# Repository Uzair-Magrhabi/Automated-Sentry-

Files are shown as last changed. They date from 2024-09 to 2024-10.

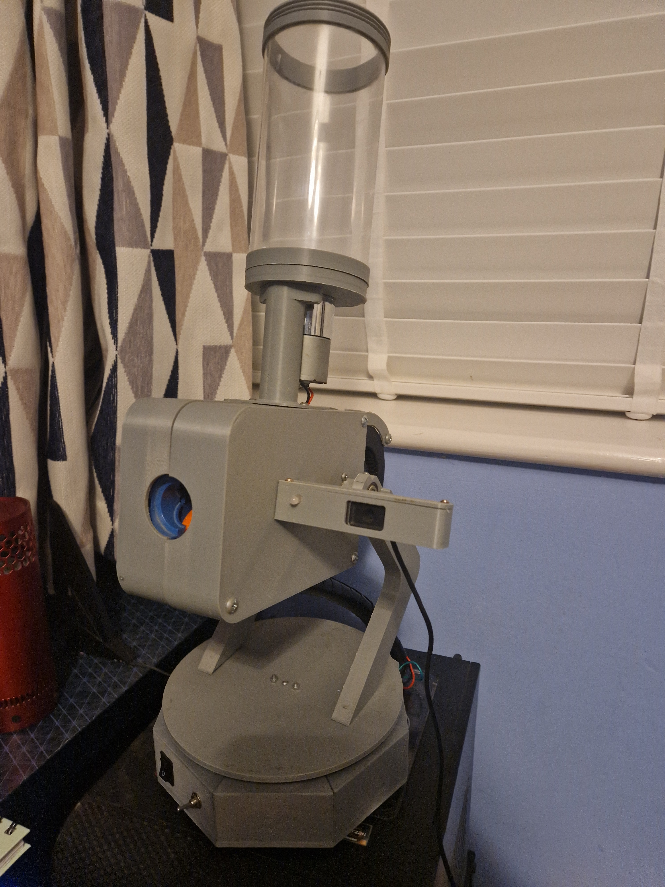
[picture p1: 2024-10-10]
20241010_222017.jpg

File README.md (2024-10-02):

Automated Sentry System
Using Fusion 360, I designed the primary firing mechanism for the turret. The propulsion system utilises flywheels, adapted from a Nerf blaster, to launch foam projectiles. A 5V blower fan is employed to feed the projectiles into the flywheels, guided by a custom-designed pipe, also created in Fusion 360. To manage projectile flow and prevent blockages, a 5V mini servo is integrated into the firing component, controlling the entry of rounds into the chamber.

The projectiles are stored in a hopper positioned above the main chassis, which can be easily refilled via a screwable lid. A custom-built propellor which acts as an agitator, attached to a coupler and powered by a high-torque DC motor, pushes the projectiles into the firing chamber when the mini servo is retracted. The hopper enclosure is transparent, allowing visual monitoring of the remaining ammunition.

Mounted on the main chassis is a camera holder, crucial for running object detection algorithms. The holder also contains an RGB LED, soldered to a PCB with the appropriate resistors, which visually indicates the system's operational states (shooting, searching, loading).

The chassis is supported by two legs: one leg incorporates a 25kg servo motor for vertical rotation, while the other includes a bearing to ensure smooth motion when adjusting the turret's elevation. These legs are fixed to a custom-designed base plate, which allows for horizontal rotation via a servo. Steel ball bearings are integrated beneath the plate to facilitate smooth, free movement.

The base houses the electronics, drawing 7V from the power supply to operate the two high-torque servo motors and the flywheel motors. A flyback diode is installed across the flywheels to prevent back-voltage, while two bypass capacitors are used to minimise electrical noise, ensuring stable operation. A diode reduces the voltage to 6.3V for powering the mini servo. Both the flywheels and high-torque motor are controlled through a relay, which can be triggered by the Arduino.

The Arduino is mounted on a separate stripboard, where all grounds and input connections are organised. The system features two switches: one is a power switch that cuts the circuit’s power, and the other is an SPDT switch connected to the A4 pin on the Arduino, allowing the signal to either pull up to 5V or pull down to 0V depending on the switch position.

The image processing is carried out on my laptop using OpenCV, a powerful computer vision library. This process involves capturing frames from a video stream (in this case, a webcam feed), detecting objects within those frames, and analyzing the position of a person relative to the centre of the image. The system implements a closed-loop visual control system, where real-time feedback from the camera is used to continuously adjust the camera's orientation based on the detected person's location.

****

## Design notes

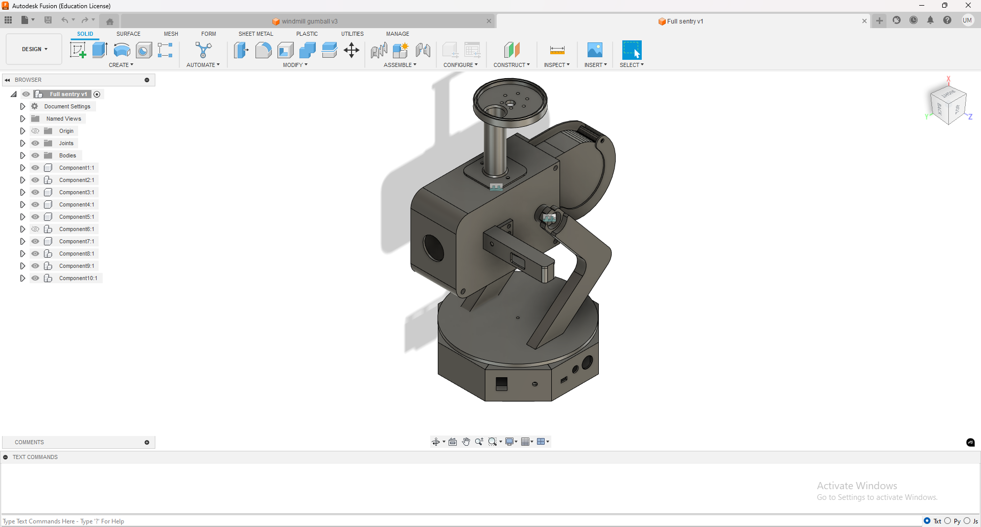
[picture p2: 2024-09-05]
Sentry.png

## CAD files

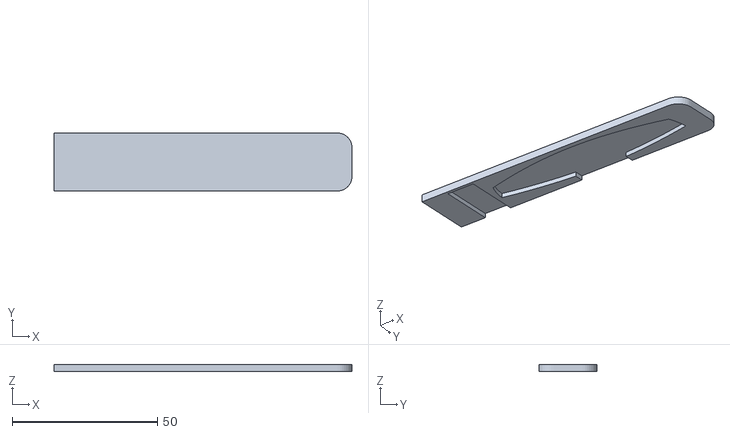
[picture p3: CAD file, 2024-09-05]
camera cover.stl
102.8 x 20.0 x 2.50

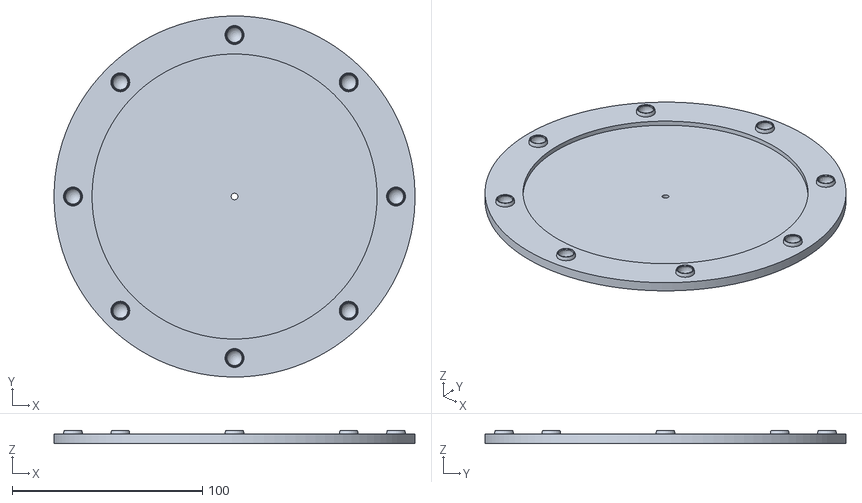
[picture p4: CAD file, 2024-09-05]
rotating disk.stl
190.0 x 190.0 x 7.00

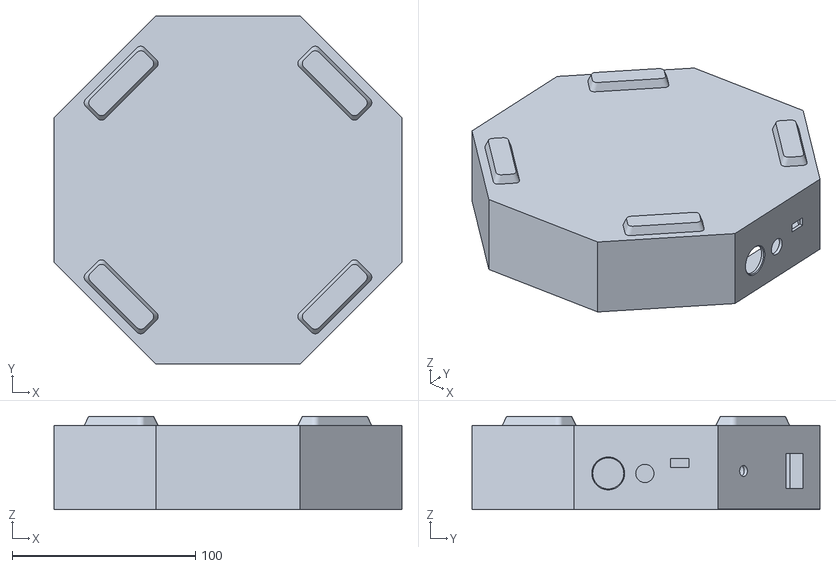
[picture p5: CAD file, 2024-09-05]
base.stl
190.0 x 190.0 x 51.0

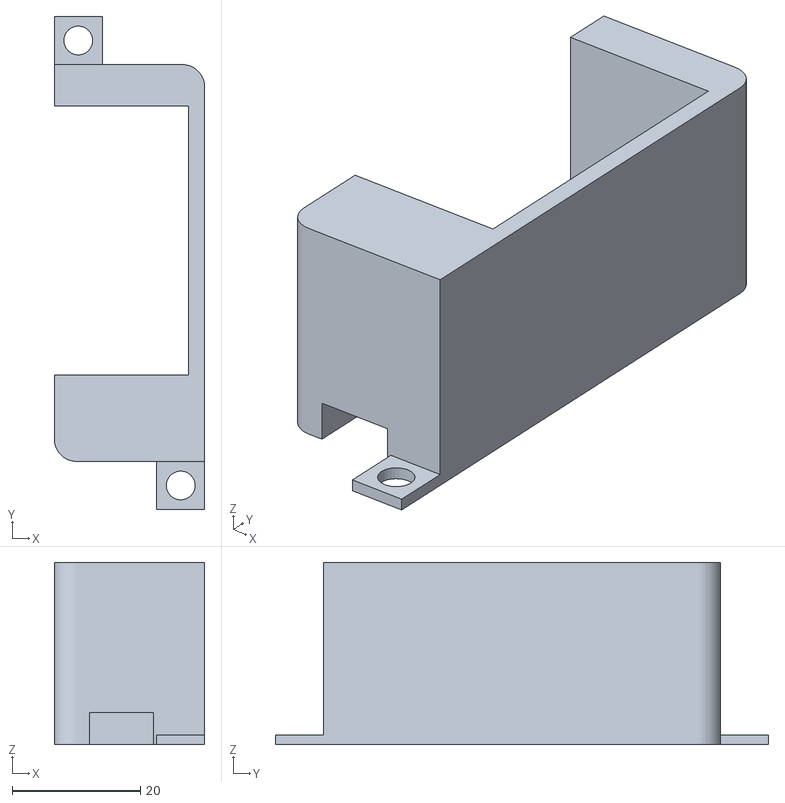
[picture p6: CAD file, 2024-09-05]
servo holder.stl
23.5 x 77.0 x 28.5

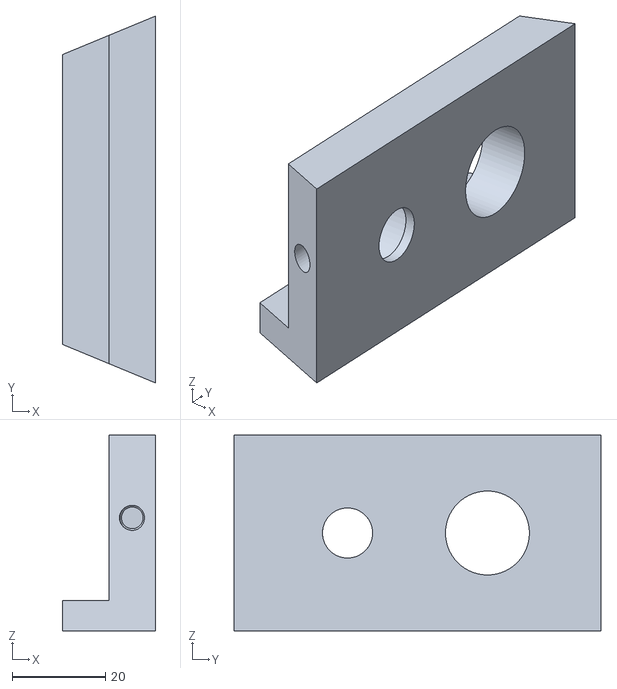
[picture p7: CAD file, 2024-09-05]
wall - cables.stl
20.0 x 78.7 x 42.0

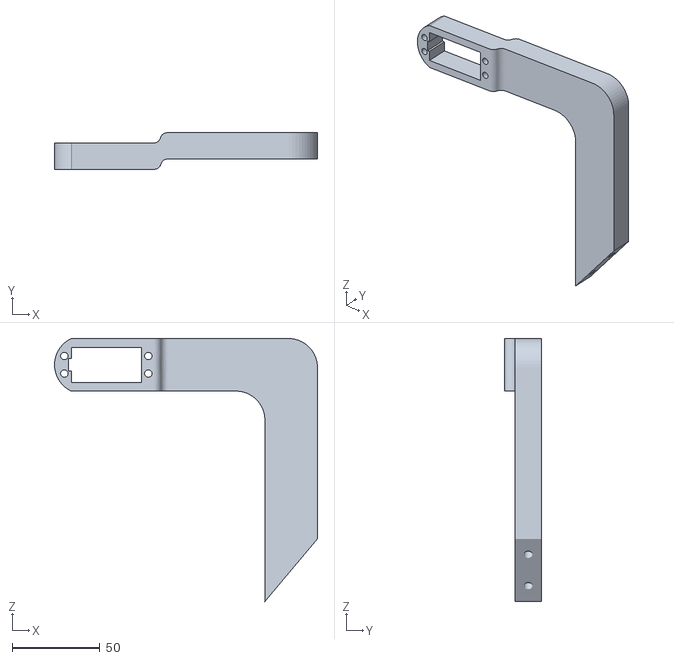
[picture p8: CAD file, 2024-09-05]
Servo Arm.stl
150.0 x 20.9 x 150.0

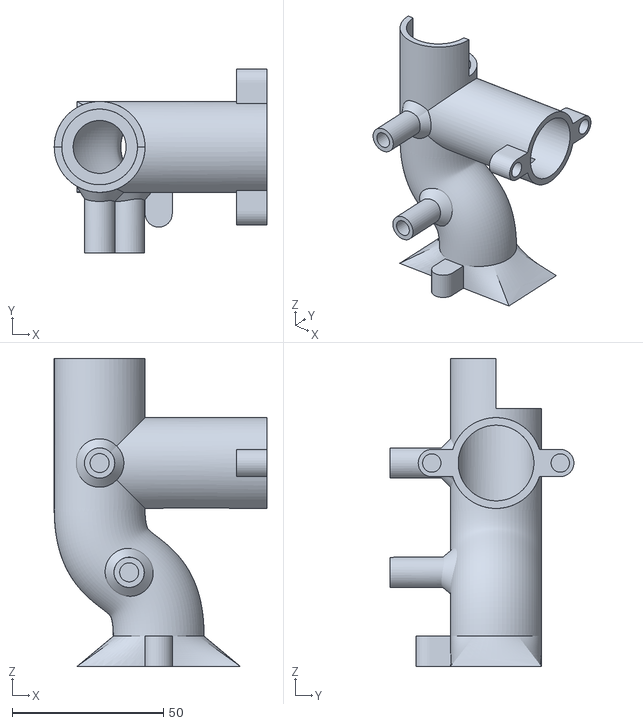
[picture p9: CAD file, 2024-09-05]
pipe.stl
70.2 x 60.7 x 101.7

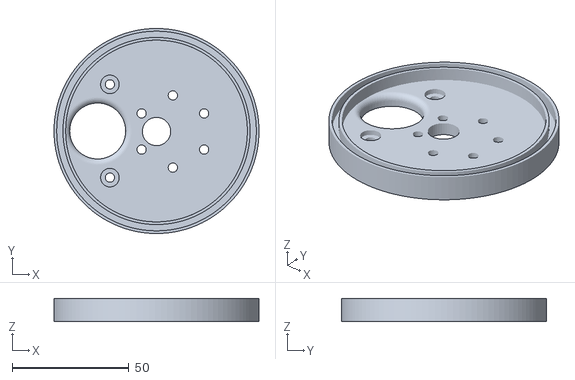
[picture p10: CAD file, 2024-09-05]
hopper.stl
88.0 x 88.0 x 10.0

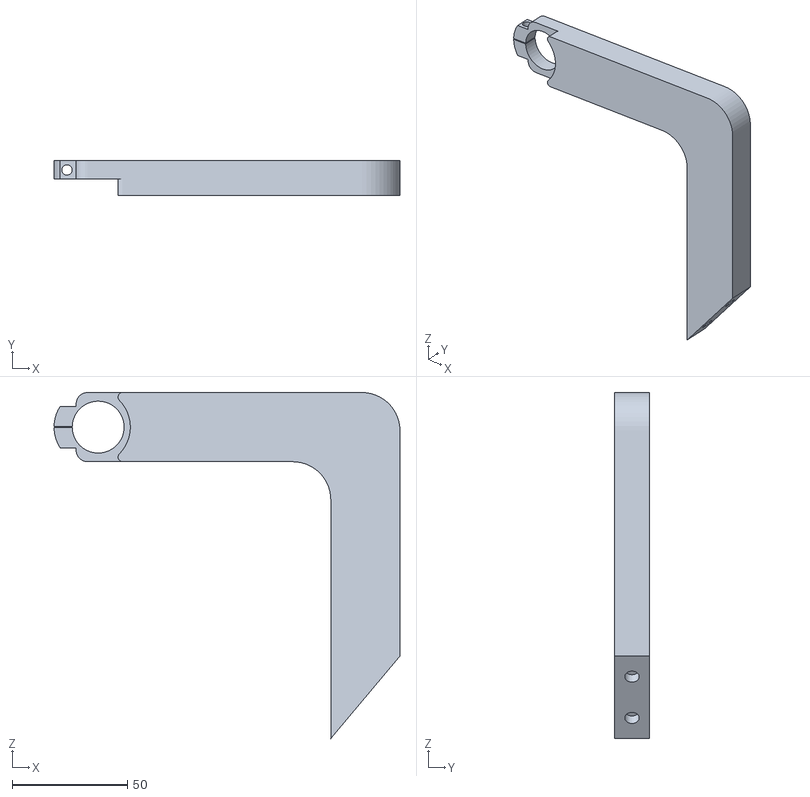
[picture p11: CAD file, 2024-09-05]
bearing arm.stl
150.0 x 15.0 x 150.0

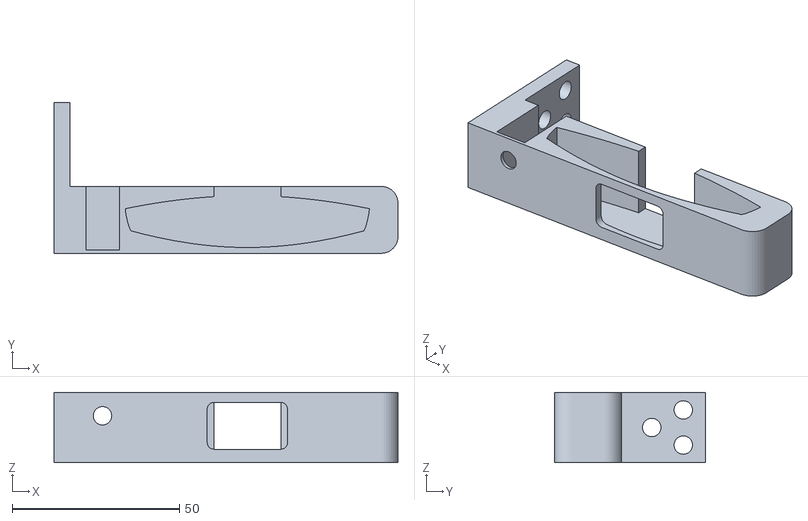
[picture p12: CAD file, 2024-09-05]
camera holder.stl
102.8 x 45.0 x 21.0

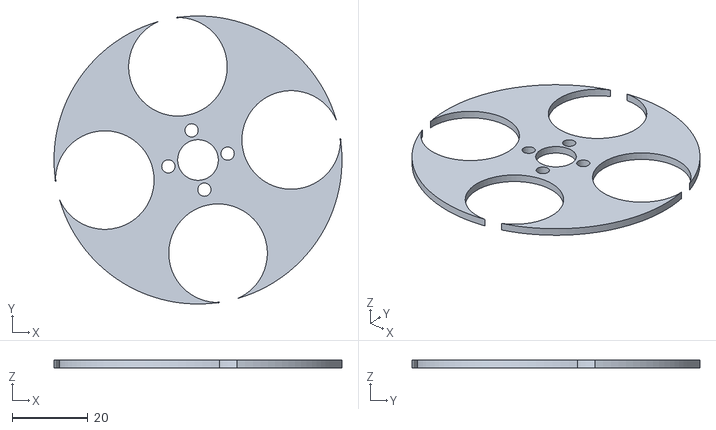
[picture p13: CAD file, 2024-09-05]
disk.stl
76.0 x 76.0 x 2.00

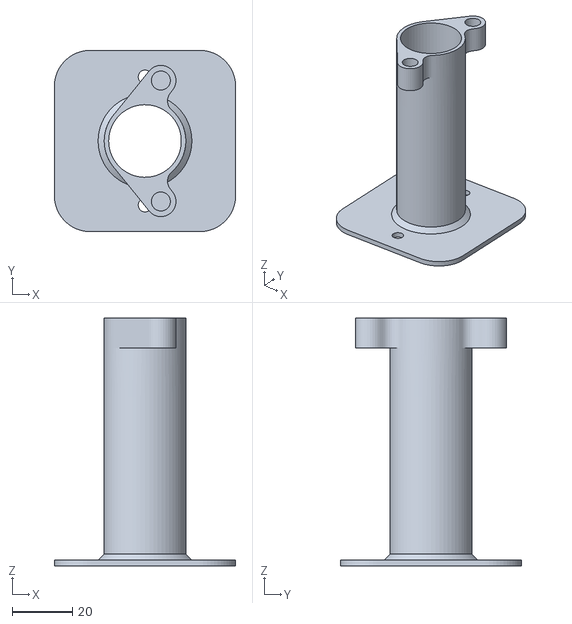
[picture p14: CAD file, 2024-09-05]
funnel.stl
60.0 x 60.0 x 82.0

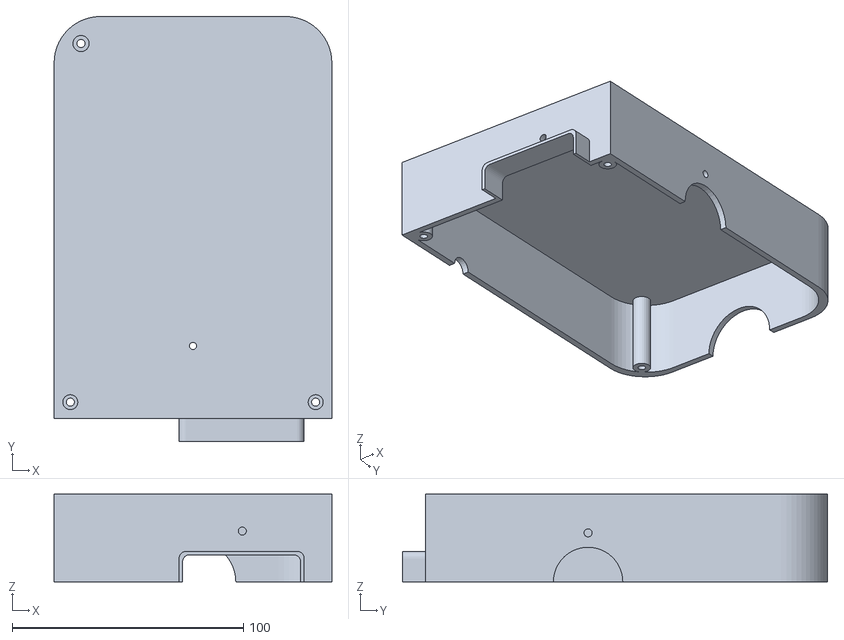
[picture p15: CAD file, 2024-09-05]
Body R.stl
120.0 x 183.6 x 38.0

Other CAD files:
Body L.stl

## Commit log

2024-09-12 Create Arduino code
2024-09-12 Update Arduino code
